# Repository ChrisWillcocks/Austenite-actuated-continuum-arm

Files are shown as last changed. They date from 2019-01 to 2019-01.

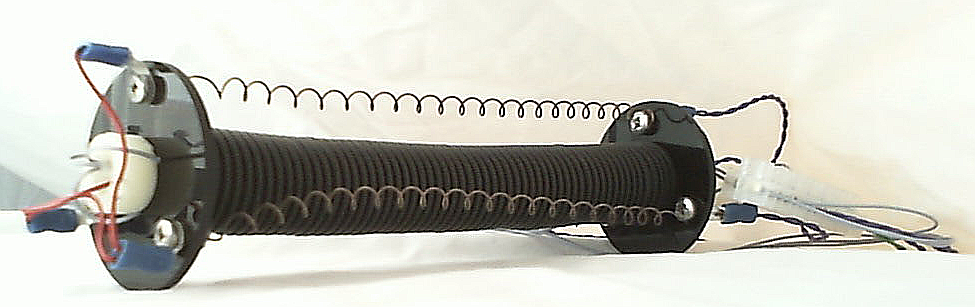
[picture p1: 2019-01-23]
hardware/snake-segment.png

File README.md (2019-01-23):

# Austenite-actuated-continuum-arm

Thesis for my MSc. Project used nitinol shape memory alloys as novel actuator for a modular snake arm robot. Thesis presents background, methods, testing and results.
Nitinol actuators are completely silent, extremely compact, and cost is comparable to existing electrical motors.

Modular chassis designed in FreeCAD. Basic testing software programmed on Arduino in C, electronic diagrams included.

Key conclusions are
- Best SMA actuators are bundles of thin (150um) wires. 
- SMAs can be modelled as a spring whose spring constant is a function of austenite to martensite ratio. Suitable for compliant actuators.
- Austenite ratio is a function of input power.
- Austenite ratio can be measured via electrical resistance (though exceptionally noisy). 3rd order elliptical filter found to reduce noise effectively.
- Heat hysteresis, the biggest drawback of SMAs, can be partially overcome with antagonistic pairs and optimal heating algorithms.
- Coil-type actuators provide largest stroke, but tend to keep heat inside the coil, exacerbating hysteresis. Improved cooling strategies could mitigate this.

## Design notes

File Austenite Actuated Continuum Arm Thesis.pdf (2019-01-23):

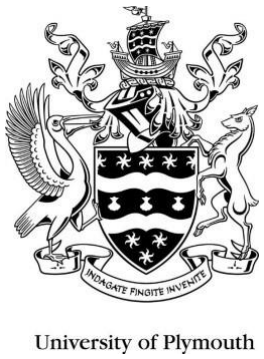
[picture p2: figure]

# Austenite Actuated Continuum Arm

# Chris Willcocks

### Supervisor: Dr D. Jenkins

## A thesis submitted to Plymouth University in partial fulfilment of the requirements for the degree of: Master of Science, Robotics

September 2018

School of Computing, Electronics, and Mathematics Faculty of Science and Engineering

Acknowledgements

I would like to extend my gratitude to Dr David Jenkins for his timely advice and invaluable

guidance across this project as supervisor.

I would also like to extend my thanks to the technicians of Smeaton Labs, for their technical

guidance.

### Declaration

________________________________________________________________

I confirm that I have read and understood the Plymouth University regulations relating to Assessment Offenses and that I am aware of the possible penalties for any breach of these regulations. I confirm that this is my own independent work.

Candidate’s Signature:

Chris Willcocks | Date: 2nd September 2018

Supervisor’s Signature:

Date:

Second Supervisor’s Signature:

Date:

### Copyright & Legal Notice

This copy of the dissertation has been supplied on the condition that anyone who consults it is understood to recognize that its copyright rests with its author and that no part of this dissertation and information derived from it may be published without the author’s prior written consent.

The names of actual companies and products mentioned throughout this dissertation are

trademarks or registered trademarks of their respective owners.

Abstract

Electric motors have been the de-facto standard actuator for robotics for close to half a century.

They offer high efficiency, torque, speed and extensively developed controllability. However,

miniaturisation is challenging, and dynamic factors such as collision response bandwidth are

limited, which pose major issues for safe human-robot interaction and operation in confined space.

In this work the viability of nitinol as an actuator in a continuum arm is investigated.

The main issues in using nitinol as an actuator are slow response due to hysteresis, very low

efficiency, low strain recovery and control of actuation.

The goal of the project is to produce an initial prototype as a functional test-bed for nitinol

actuation and future experimentation, as well as investigate the mechanical and electrical properties

of a nitinol actuator. To maximise strain recovery a coil type actuator was chosen, which has the

drawback of an inconsistent coil pitch during the cooling cycle. Methods to mitigate this are

proposed.

Experiments to characterise the mechanical and electrical properties of the nitinol sample were

performed.

Actuation is a function of martensite to austenite crystal ratio, which can be detected by

electrical resistance. Experiments were conducted to determine the resistance response across

actuation cycle, and in general were found to have a negative coefficient. However, significant

noise is encountered, which complicates using resistance as a sensing signal.

Finally, a number of recommendations are made for future study.

Contents

Abstract
4

Introduction
8

Outline
9

Chapter
1
– Literature review | 10
Discovery of the shape memory effect | 10
Basic principles | 10
Phase changes | 10
Structure | 11

Pseudo

-elasticity | 12
Current uses | 12
Major limitations | 13

Chapter
2
– Controller development | 15
Introduction | 15
Method | 15
Temperature sensing | 16

Micro

-controller | 16
Driving current | 17
Measuring resistance | 17
Testing | 1
| 8
Driver | 18
Temperature | 18
Resistance | 18
Results | 20
Driver | 20
Resistance | 22
Discussion | 23
Conclusion | 24

Chapter
3
– Characterisation experiments | 25
Introduction | 25
Method | 25
Introduction | 25
Stress / strain | 25
Resistance response | 26

Filtering | 26
Results | 27
Resistance response | 27
Stress / strain | 28
Filtering | 30
Interval average | 30
Exponential filter | 31
Running average | 31
Discussion | 31
Resistance to temperature | 31
Stress / strain | 32
Filtering | 33
Conclusions | 34

Chapter
4
– Single segment | 36
Introduction | 36
Construction | 36
Spine | 36
Sensor design | 37
Testing | 38
Results | 38
Discussion | 40

Conclusio
n | 42

Chapter
5
– Project results | 43
Controller design | 43
Electrical resistance | 43
Continuum segment | 44

Chapter
6
– Project discussion | 45
Modelling | 45
Limitations | 45
Recommendations | 46

Chapter
7
– Project conclusions | 47
References | 49
Appendices | 51

List of Figures

Figure 1 – Actuator comparison | 13
Flowchart 1 – Main Loop | 18
Flowchart 2 – Read Temperature function | 18
Flowchart 3 – Read Resistance function | 19
Flowchart 4 – Read Position function | 19
Flowchart 5 – Set Position function | 19
Figure 2 – Temperature rise response | 21
Figure 3 – Temperature hold 40 Celsius experiment 1 | 22
Figure 4 – Temperature hold 40 Celsius experiment 2 | 22
Figure 5 – Temperature hold 40 Celsius experiment 3 | 23
Figure 6 – Temperature hold 50 Celsius experiment 1 | 23
Figure 7 – Temperature hold 50 Celsius experiment 2 | 24
Figure 8 – Temperature hold 50 Celsius experiment 3 | 24
Figure 9 – Temperature hold 60 Celsius experiment 1 | 25
Figure 10 – Temperature hold 60 Celsius experiment 2 | 25

Figure 11 – Temperature hold 60 Celsius experiment 3

26

Table 1 – Hysteresis overshoot | 26
Figure 12 – Resistance response to temperature sweep | 32
Figure 13 – Stiffness against temperature | 33
Figure 14 – FFT Frequency response | 34
Figure 15 – Low pass filtering | 35
Figure 16 – Interval average filter | 36
Figure 17 – Exponential average filter | 36
Figure 18 – Running average filter | 37
Figure 19 – Spine segment assembly | 43
Figure 20 – Spine segment prototype | 44
Figure 21 – Bend sensor assembly | 45
Figure 22 – Bend sensor motion response 1 | 47
Figure 23 – Bend sensor motion response 2 | 47
Figure 24 – Bend sensor motion response 3 | 48
Figure 25 – Displacement at 30 Celsius | 59

Figure 26 – Displacement at 35 Celsius | 59
Figure 27 – Displacement at 40 Celsius | 59
Figure 28 – Displacement at 45 Celsius | 59
Figure 29 – Displacement at 50 Celsius | 59
Figure 30 – Displacement at 55 Celsius | 59
Figure 31 – Displacement at 60 Celsius | 59
Appendix A – Controller circuit diagram | 60
Appendix B – Driver circuit diagram | 60
Appendix C – Thermistor circuit diagram | 60

Introduction

In 1958, dismayed at mountains of obsolete tooling, inventor George Devol was inspired to

develop a reusable machine. His eventual creation, the Programmable Article Transfer the

“Unimate” was used to move parts on car assembly lines, and revolutionised industry. At the time,

electric motors could not provide an adequate solution for the Unimate owing to insufficient power

density, and so the Unimate was a hydraulic machine, which “leaked like a sieve”. Despite these

issues, the Unimate was a huge success, and remained the de-facto industrial robot until the

development of the Stanford arm. The Stanford arm was a purely electric robot, and was portable

enough to take to interview, where its abilities to move precisely into position using inverse

kinematics gave a significant advantage over existing hydraulic machines.

Over more than half a century, robots have cemented themselves in industrial applications,

where their repeatability, precision, and endurance have proved invaluable. However, robots have

largely stayed in these positions.

Two major limiting factors are size and power output (O’Toole, 2011). Standard electric motors

have undergone significant miniaturisation, even to the point of single molecule motors, but this

results in reduced power output.

Partial solutions to this problem have been found, such as the Laser Snake by OC Robotics (OC

Robotics, 2012). This robot uses tendons to mechanically link a bank of remote motors to a

segmented body. This retains much of the accuracy of a standard robotic arm, while removing the

weight of electric motors from the robot body and greatly reducing the robot’s size. However, the

size is still limited by the diameter and number of tendons. Most standard motor technologies suffer

from this limitation of physical dimensions.

Other motor technologies exist alongside electric motors, hydraulics and pneumatics, such as

piezoelectric elements, ultrasonic motors and polymers, but these typically do not have the stroke or

force output to be suitable for existing robotic applications. One promising alternative actuator is

the Shape Memory Alloy (SMA). Many SMAs exist, but of particular interest, due to ease of use

and power density, is nitinol.

In terms of size and power, the shape memory alloy nitinol offers a promising alternative. As reported by Teh (2008) “shape memory alloys show one of the highest work densities at 10e7 Jm⁻³ ,

which is a factor of 25 times greater than the work density of electric motors”.

Nitinol offers a number of benefits over other actuators, primarily in terms of a very compact

form factor. Other benefits include the potential for very low power, noiseless operation (O’Toole,

2011), compliance and ease of assembly.

Despite these potential advantages nitinol suffers from a number of drawbacks which prevent more

widespread adoption, including very low efficiency, difficulty in control and significant hysteresis.

The aims of this project are to construct a prototype continuum arm and electronic controller as a

test bed for development of nitinol as a robotic actuator.

Outline

The following chapters provide background and context for the motivation and approach of this

dissertation. Chapter 2 details the construction of a high power driver with integrated resistance

sensing circuit. Chapter 3 details a number of characterisation experiments, most crucially the

resistance response across the martensite and austenite phases, and stress and strain curves. The

relationship between temperature and nitinol’s spring constant is found. Chapter 4 details how a

single segment of a continuum arm was developed, including flexible sensor feedback devices.

Experimentation to verify operation of the feedback sensors was performed. Chapter 5 details the

project results and chapter 6 presents a discussion on the findings. Finally, chapter 7 presents the

conclusions, with recommendations for future study.

Chapter 1 - Literature review

This chapter presents background and context for the project. A brief history of nitinol is first

given. The basic principles are covered, including the crystalline structure of nitinol, the low

temperature martensite and high temperature austenite phase, phase transforms including twinned

and de-twinned martensite, mechanical properties and electrical properties.

A brief introduction to existing applications is presented, including both research and

commercial efforts.

Finally, a review of major limitations to more widespread nitinol actuator usage are analysed

and discussed.

Discovery of the shape memory effect

The earliest documented discovery of the shape memory effect was recorded by Arne Olander,

a Swedish physicist. In 1932 he observed the shape memory effect (SME) in gold-cadmium.

However, shape memory alloys were not practical until the discovery of SME in nickel-titanium,

discovered partially by accident in 1961. William Buehler and Frederick Wang, working in the

Naval Ordinance Laboratory, had produced a new alloy material for rocket nose cones. During a

demonstration, a member of the audience held a small sample to his smoking pipe, and was quite

surprised when it began moving.

Nitinol began to see major applications in the 1980s, primarily in the medical sector as a result

of good bio-compatibility. Devices such as stents made use of the shape memory effect, which

could automatically expand from body temperature soon after insertion (Teh, 2008). More recent

uses include part of a tail control system in Festo’s BionicOpter dragonfly (Festo, 2011).

Although other alloys, such as Fe-Mn-Si, Cu-Zn-Ni and Cu-Al-Ni exist, “due to their

instability, impracticability (e.g. brittleness) and poor thermo-mechanic performance, NiTi-based

SMAs are much more preferable for most applications” (Jani et al., 2014).

Basic principles

Phase changes

The defining characteristic of a shape memory alloy is the shape memory effect. Put simply, a

shape memory alloy can change shape when subject to energetic events, such as thermal heating,

magnetic induction, radiation or electrical Joule heating (Kumar, 2014). This is achieved through an

ability to exist in two distinct crystal structures, the low temperature martensite phase, and the high

temperature austenite phase.

The martensite phase is characterised by a low Young’s modulus, easy deformation, low yield

strength (Jani), and higher electrical resistance (Ma, 2004) (Teh, 2008).

The austenite phase is almost the inverse of the martensite phase; a much higher Young’s

modulus, highly recoverable strain, much higher yield strength, and lower electrical resistance. The

changing electrical resistance is of particular interest, as it is a measure of the austenite to

martensite ratio, rather than the electrically induced heating (Ma, 2004).

The potential for use as an actuator exists in this phase change. During deformation in the

martensite phase, a stress will produce a strain, and the strain will remain when the stress is

removed. During the austenite heating phase, this strain can be recovered, resulting in high

actuation potential (Jani et al.).

Structure

Twinned martensite: During the austenite phase the SMA’s crystal structure changes to be cubic

(Gorbet. R, 1996), and this structure remains when cooled, resulting in twinned martensite. The

cubic, twinned martensite will undergo a process known as de-twinning when subject to an external

load, changing the cubic martensite into rhombohedral de-twinned martensite. Essentially, the SMA

must always be “pulled” into a rhombohedral structure.

At low temperatures, the SMA will consist of 100% martensite. In the case of Joule heating,

which this project investigates, the SMA must be raised to the austenite start temperature, at which

point martensite will begin changing into austenite.

At the austenite finish temperature, the SMA is 100% austenite. The SMA then needs to cool

down to the martensite start temperature for martensite to begin forming, and the SMA will be fully

martensitic at the martensite finish temperature.

Typically, the martensite and austenite start and finish temperatures do not overlap, producing a “wide thermal hysteresis loop” (Teh, 2011, pg 10).

During the martensite phase, the SMA will display characteristics of a very soft spring, and is

capable of recovering a small amount of strain. If the applied stress exceeds the martensite yield

strength, the SMA will deform plastically. Further applied stress beyond this point will again cause

the SMA to behave elastically, until a yield point, beyond which strain becomes unrecoverable (Teh,

pg 35).

One-way shape memory effect:

Most commonly, SMAs make use of the one-way shape memory effect. An external stress

induces strain, and deforms the SMA into the martensite phase. Upon application of energy, austenite forms, and the shape memory effect occurs, returning the SMA to some remembered

shape. In the case of the coil SMAs used in this project, this has the effect of reducing the coil pitch

and length (Jani et al).

Two-way shape memory effect:

Much like the one-way effect, the two-way effect will recover a shape after deformation when

energy is applied. However, upon cooling, the SMA will also recover a remembered shape. When

compared to the one-way SME, the two-way effect requires training cycles (heating to one

remembered shape, and cooling to a second), deteriorates more quickly, and produces less strain

(Jani et al.). For these reasons it is commercially less attractive.

Pseudo-elasticity

Recovered strain is observed without application of energy. Typically, this is achieved by

having the austenite start temperature somewhere below room temperature, and finds common

application in fishing lines and braces, where the robustness of nickel-titanium is highly attractive.

Other transformations exist, such as rhombohedral and bainitic transformations (Jani et al.)

(Teh), but these are beyond the scope of this dissertation.

Current uses

Nitinol currently finds a number of commercial uses. Pseudo-elastic nitinol is used a fishing

leader (maybe description?), where the highly recoverable strain prevents kinking and provides a

more robust alternative to steel leaders (edge-techind.com, 2015).

Nitinol finds extensive use in the medical industry, where its physical properties and excellent

bio-compatibility are highly beneficial. Stents can be set to have an austenite finish temperature

matching internal body temperature, providing easy martensite insertion, and automatic expansion

when at the target site. However, these applications are essentially single-use, passive applications

of nitinol. Other applications making active use of nitinol include the Festo BioniCopter, which uses

nitinol elements to control the tail for lightweight, in-flight manoeuvrability. Use in aeroframes in

the pseudo-elastic phase has been achieved for vibration damping (Zhang et. al, 1996).

Compared to other technologies, nitinol is capable of producing significantly more stress than

even hydraulic actuators as a function of weight, though the potential of scale is uncertain, a

significant work volume, and a power volume greater than other actuators with the exception of

piezoceramics (Jani et al., pg1082).

O’Toole has investigated the use of nitinol in prosthetic limbs as a small-profile actuator, due to

nitinol’s low weight, high energy density, ease of integration, and silent operation.

His findings and conclusions are that force output from nitinol increases as per area, but so does

required current. Therefore, nitinol size selection should be determined by transient response to

applied current. Thinner wires appear to be a generally better approach, as thicker wires have

“severely diminished performance during natural cooling activity with significant relaxation times

evident”. Improved performance was seen in larger bundles of smaller wires, and a time delay “of

0.1-0.3 seconds” has been reported.

Interestingly “maximum strain is independent of wire diameter”, which implies a very small

necking region before unrecoverable damage is incurred. More predictably, as straight wire nitinol

was used, recoverable strain was relatively low, as O’Toole reports “strain observed in bundles is

approximately 3.6%”.

Holschuh et al (2014). have investigated the use of SMAs in active compression garments.

Their approach was to use coil actuators, which was found to produce “large recoverable

displacements (>100% in length)”.

Their findings are that “low spring index NiTi coil actuators … can produce large

displacements and… forces in a form factor that closely resembles a typical textile fibre”.

Major limitations

A nitinol actuator offers unparalleled advantages in terms of size and power to weight ratio, but

currently suffers from several severe drawbacks. The most pressing of these issues are low

recoverable strain, low accuracy, very low efficiency, controllability, and low actuation frequency

(Jani et al.)

Low strain

Figure 1 - actuator comparison

Strain within a straight nitinol wire is quite low. Plastic deformation will occur at 8% (Teh), and

most applications will keep strain well below this limit, often at 4% or less, as reported by O’Toole

with straight wire actuators. Holschuh et. al have demonstrated a solution to this issue through the

use of coil-type actuators, however Jani notes that this geometry of nitinol suffers from inconsistent

uncoiling.

Low accuracy

Teh reports that considerable improvement in nitinol control has been achieved, primarily

through PWM, PID and feed-forward control, however, the main limitations come from

“nonlinearities such as backlash-like hysteresis and saturation effects”, which are inherent to nitinol

and difficult to account for in any control system. This is also reported by Lange, G et. al(2015),

who conclude using an adaptive PID controller can compensate for the non-linear behaviour of the

material.

Low efficiency

As a heat activated SMA is a essentially just a heat engine, the maximum efficiency is

determined by the temperature delta. As an example, if a nitinol sample achieves austenite finish at

353k, and martensite finish at room temperature of 298k, the absolute maximum efficiency would

be 15.58%. This is before considering other inefficiencies, such as losses to atmosphere,

inefficiencies in power supply, and control limitations.

As reported by Jani et al. “Theoretically the maximum energy efficiency of SMAs is in the

range of 10–15%, which may fall to 10% based on the Carnot cycle efficiency in some studies, and

is often less than 1% in practical applications”.

Slow response

One of the most significant drawbacks with an SMA actuator is the very slow response, the low

actuation frequency and narrow bandwidth. The issue again lies primarily with nitinol being a heat

engine. Several studies (Qiu, 2001, Featherstone, 2006, Chee, 2005) have found that applying large

currents can overcome the slow heating phase. Another approach is to use nitinol with small volume

to surface area, as reported O’Toole and supported by Jani. However, the cooling phase is still

problematic, owing to the need for the heat to disperse through the body of the SMA via the surface

area. According to Jani et al. “the most significant concern in band-width limitation is the very slow cooling process, where the heat energy removal rate is limited by the mechanisms of heat

conduction and convection.”

Many studies have investigated resolving this issue, including using conventional heat sinks,

Peltier devices, convective cooling (air and liquid), and passive cooling. Although each approach

does improve performance, the trade-off is often in additional mechanical complexity, noise, energy

requirements, size and weight, all factors which SMA actuators are generally selected for.

Long-term life

Care must be taken when straining SMAs, and all SMAs suffer from life-cycle limits. Straight-

wire SMAs can recover 4% strain, and when pre-loaded, can recover up to 7% by pre-straining.

However, previous studies have found that overstraining nitinol results in reduced stroke over

operational lifespan. As reported by Jani et al. “SMAs have been shown to exhibit a softening of

behaviour (i.e. reducing the amount of recoverable strain) as the actuator is cycled, … by heating

and cooling the SMA under load”.

For this reason, keeping stroke and strain within operational limits is of vital importance.

Chapter 2 – Controller development

Introduction

In this chapter the development of a nitinol controller is detailed. A high power driver is

implemented using an N-channel MOSFET, and a programmable micro-controller used to modulate

applied power. A temporary thermistor is used to detect temperature changes for experimentation

and avoid overheating the nitinol. A resistance sensing circuit is developed to test the viability of

using resistance as a feedback mechanism for current control.

Method

A primary goal of this research is to develop a controller suitable for use with a nitinol actuator.

Currently, no commercial-off-the-shelf solutions exist for driving nitinol. As such, a major

focus of this project will be in the design and implementation of suitable driver circuitry. To achieve

this, two sub-circuit elements will be developed: the first will be a driver capable of delivering high

current to the nitinol element, the second will be a sensing circuit which will determine resistance

across the nitinol. During development, measuring temperature directly will also be necessary, as

resistive values for martensite and austenite phases are not typically available.

Once the hardware is constructed, a suitable control method will be implemented. The initial

control methodology will be a bang-bang driver. This simple approach has been chosen for rapid

development, but will also allow for measurement of nitinol’s heat cycle response to input power,

and allow for measurement of the resulting time lag. This simple control methodology would be

unsuitable for more advanced use, such as positioning.

The nitinol must not be overheated. Initially, the temperature will be monitored with a

thermistor, as this will produce more accurate and more reliable results than measuring resistance,

and does not require calibration or tuning. This has the obvious limitation of being unable to check

temperature across the entire length of the nitinol coil. To overcome this during initial

characterisation experiments, the thermistor will be inserted through the centre of the coil, and the

coil hung vertically. This will aim to minimise temperature read errors.

Ultimately, a better approach to preventing overheating is required. As reported by Ma,

resistance varies with the changing ratio of austenite to martensite. Measuring resistance therefore

gives indication of phase state, and is robust against external factors like ambient temperature,

although the relationship is highly non-linear.

Temperature sensing

One issue of concern with nitinol is overheating. As reported by Jani and Teh, if the nitinol is

allowed to overheat, degradation of the shape memory effect can occur with extended usage. To

prevent this, careful monitoring of the temperature must be achieved.

At the project outset, measurement of resistance was selected as an approach to measure

temperature. This was to then be used to control the nitinol phase state, after determining the

austenite and martensite start and stop temperatures. However, according to Ma, the resistance is

actually a function of the proportion of martensite to austenite. This actually proves beneficial, as

the need for extrapolation is removed, and phase change can be measured directly. In theory, by

measuring when the resistance change stops, the austenite finish temperature can be determined,

and the heating phase can be optimised. This relationship can then be used to control applied power,

applying only as much power as necessary to bring the nitinol to the austenite finish temperature.

This will be more fully explored in chapter 3.

Feedback on the temperature of the nitinol still remains vital, in order to prevent overheating.

Initially, a thermistor will be used, which proved to be an appropriate approach while the nitinol

was kept in the coiled state, and the entire element was be in close proximity to the thermistor.

However, as the nitinol will be stretched when mounted on the continuum arm the thermistor will be unable to effectively read the temperature across the entire nitinol sample. As such, the relation

between temperature and resistance will be investigated in chapter 3.

Micro-controller

A suitable micro-controller needs to be selected for centralised control of the driver. The micro-

controller must be able to transmit data to a computer for further processing, have access to a

number of analogue inputs, and be capable of producing PWM drive signals. Sufficient code space

so as to allow for flexible development will also be beneficial. For these reasons, the Atmega328

was chosen as the primary development platform.

Driving current

Nitinol, in both phases, has very low resistance. The martensite phase was measured at 1.5ohms

on delivery. Teh reports the use of high currents, both to overcome the slow heating cycle, and to

provide large actuation forces. Therefore, the most appropriate driver would be a power MOSFET,

capable of handling high current, with a very low Rds-on value. As the MOSFET will be passing

large current values, a MOSFET which can easily be driven to saturation from the ATmega328 will

be necessary.

The nitinol sample’s resistance is very low, measuring 1.5 ohms when fully martensitic at room

temperature. Nitinol typically requires high current to operate as well, meaning that any switch must

have a very low on resistance. For these reasons, the IPP072N10N MOSFET was selected, owing to

an Rdson of 7mOhms and a gate threshold voltage of 3.5V, allowing for easy saturation driving. N-

channel MOSFETS are easier to source, therefore the driver circuit was designed as a low-side

switch.

Owing to the low electrical resistance of nitinol, the driver circuitry will not need to provide a

high voltage. For initial testing, a 1A supply will be used, which would thus only require 1.5 volts

to conduct. This will later be increased to 3A, which is the highest current that can be driven from a

5V supply. The earliest prototype test driver, driven by the supply voltage, drew only 3.6V, only just

turning the MOSFET on. This was remedied once the micro-controller was used to drive the

MOSFET.

Measuring resistance

The analogue pins of the Atmega328 are only capable of measuring voltage. Therefore, to

measure the resistance through the nitinol, each nitinol element was built into a voltage divider. To maximise sensitivity, the sensing resistor was chosen to be a close match to the measured resistance

value of 1.5 ohms. Due to this low resistance the sensing resistor resistor will experience a high

current and there exists a potential risk of overheating. Therefore, the sensing resistor’s power

rating will need to be a minimum of 5W, and the closest commercial solution was 7W. For

simplicity of construction, the driving voltage will also be used as the testing voltage. The testing

sub-circuit must be activated periodically, to prevent the sensing resistor from overheating.

Although this approach reduces accuracy, construction is greatly simplified.

The micro-controller’s built-in ADC has a resolution of 10 bits, allowing for a sensitivity of

0.0049V. This can be improved by using the internal 3.3V supply as a reference voltage, increasing

sensitivity to 0.0029V. The current PSU is capable of supplying 1A, which for the 1.5ohm nitinol

will require a maximum of 1.5V, well within the saturation range the 3.3V reference voltage causes.

The circuit diagram can be found in appendix A.

Algorithm

The algorithm for the experimental driver follows the flowchart listed below. As temperature

sensing via the thermistor is unsuitable during standard operation this is considered a non-

mandatory process.

The nitinol resistance is also unsuitable for use as a positional feedback sensor, as resistance is

dependent on crystal formation, which is independent of machine position. Therefore, a position

sensing subroutine is implemented. The development of the sensor type is described in chapter 4.

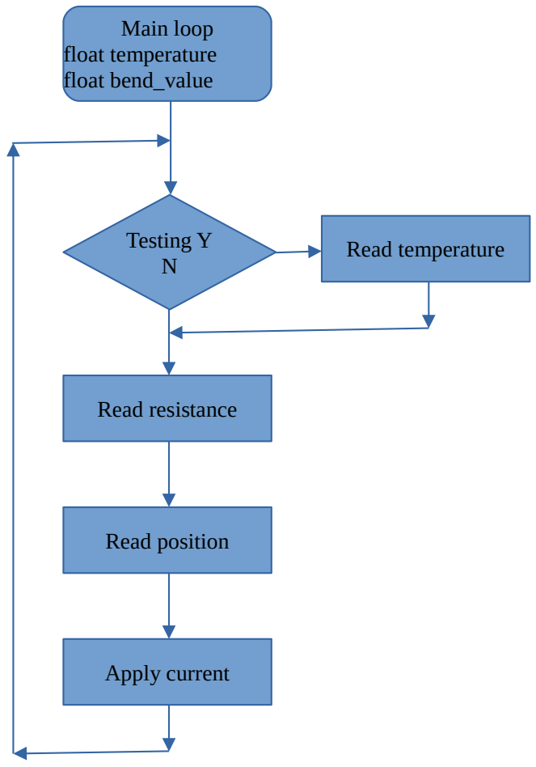
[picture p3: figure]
Main loop float temperature float bend_value; Testing Y N; Read temperature; Read resistance; Read position; Apply current
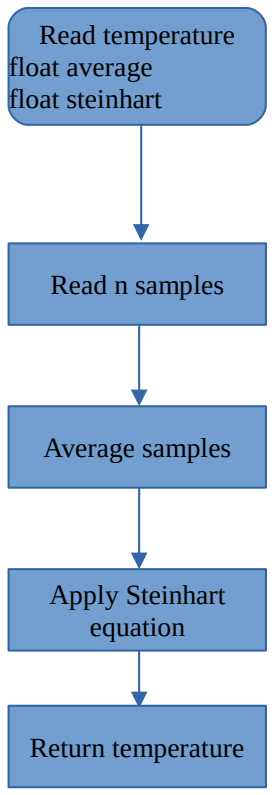
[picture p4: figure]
Read temperature float average float steinhart; Read n samples; Average samples; Apply Steinhart equation; Return temperature
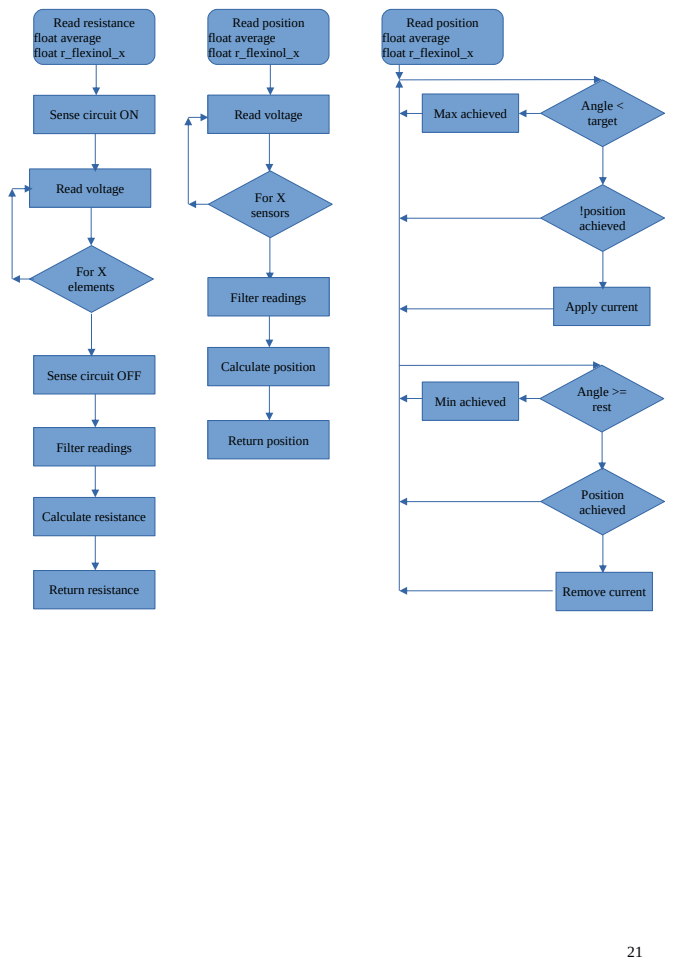
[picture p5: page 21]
Read position float average float r_flexinol_x; For X sensors; Read voltage; Filter readings; Calculate position; Return position; Read resistance float average float r_flexinol_x; For X elements; Calculate resistance; Return resistance; Max achieved; Angle <; target; !position achieved; Apply current; Position achieved; Angle >= rest; Remove current; Min achieved

Sense circuit ON

Sense circuit OFF

Testing

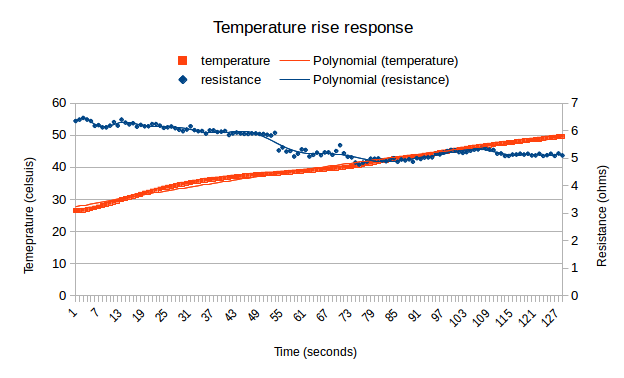
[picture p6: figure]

Driver

After circuit assembly and continuity checks driver operation was assessed by connecting a

sample of nitinol and checking for current flow and temperature increase using the thermistor.

Temperature

The heating capacity of the driver circuit, the accuracy of the resistance sensing circuit, and the

heat capacity of the nitinol were tested. A simple bang-bang controller was used, first to bring the

nitinol to a target temperature, and then to hold at the specified temperature. An additional benefit

of this simple control scheme is the ability to observe temperature lag through the nitinol sample.

The expected heat response would be an oscillation around the target temperature. The resistance

was expected to change during the heating phase, and remain unchanged during the cooling phase,

as no external load will be applied.

A nitinol sample was received in the zero-pitch configuration and connected to the test driver.

The thermistor was inserted through the centre of the nitinol to obtain an even sampling of heat. A

simple bang-bang controller was written to bring the nitinol sample to a selection of temperature

increments, hold at the target temperature, and record resistance.

Figure 2- temperature rise response

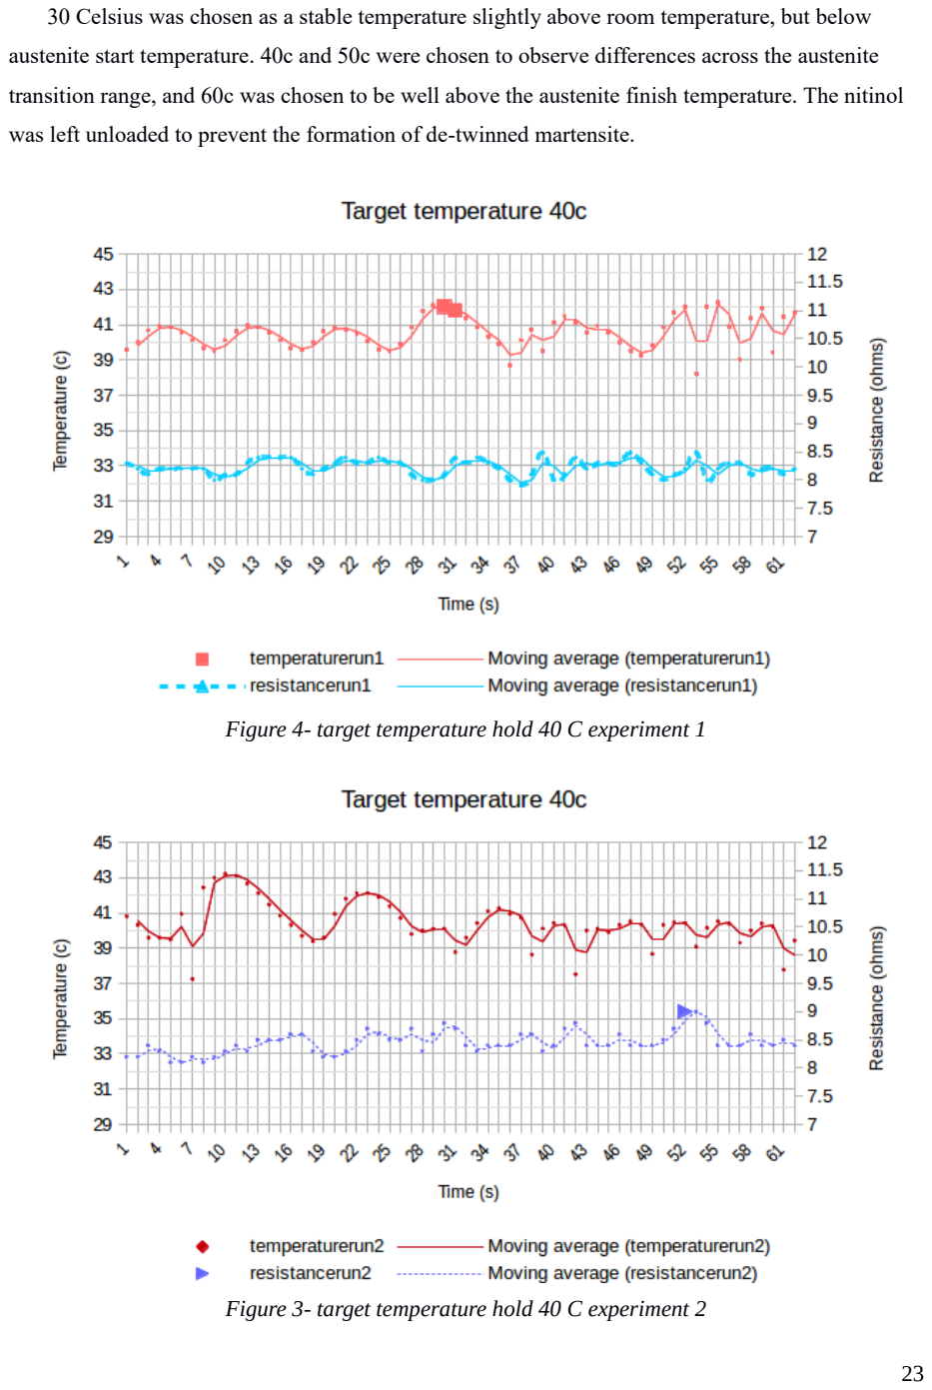
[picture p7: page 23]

30 Celsius was chosen as a stable temperature slightly above room temperature, but below

austenite start temperature. 40c and 50c were chosen to observe differences across the austenite

transition range, and 60c was chosen to be well above the austenite finish temperature. The nitinol

was left unloaded to prevent the formation of de-twinned martensite.

Figure 4- target temperature hold 40 C experiment 1

Figure 3- target temperature hold 40 C experiment 2

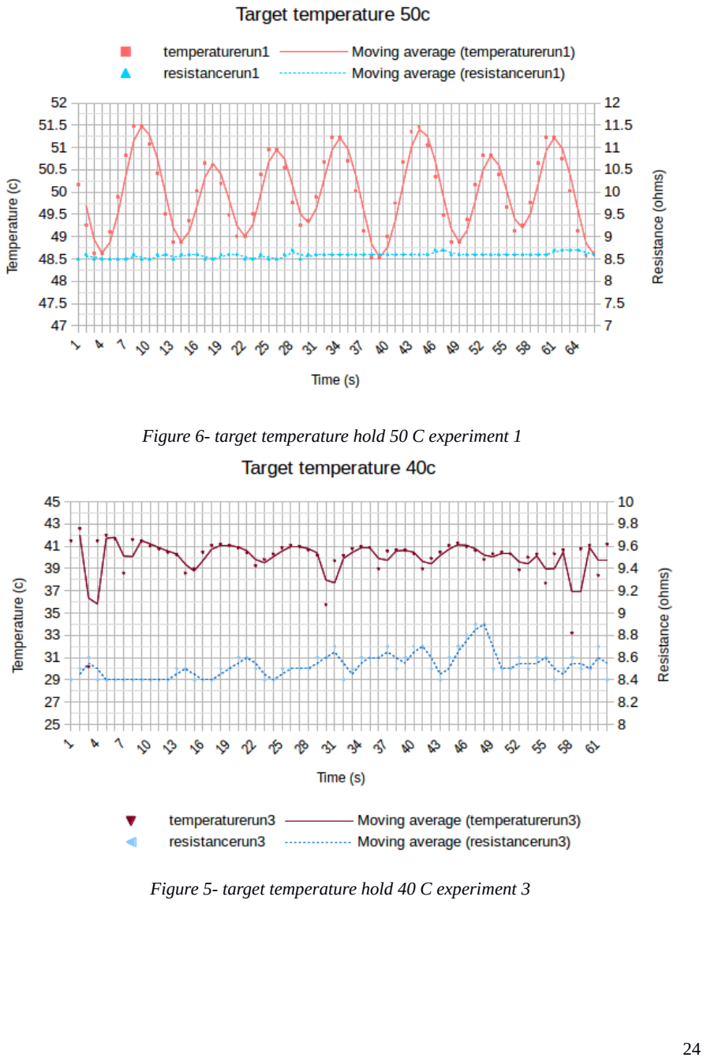
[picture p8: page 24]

Figure 5- target temperature hold 40 C experiment 3

Figure 6- target temperature hold 50 C experiment 1

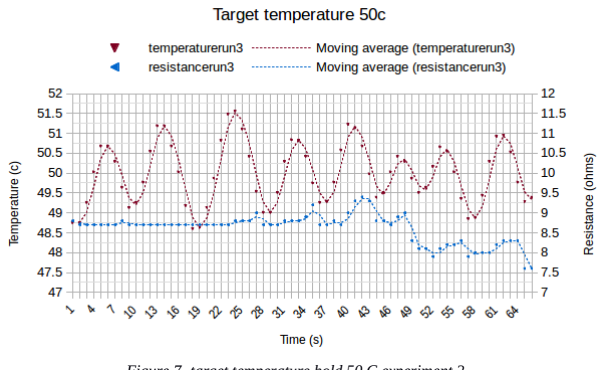
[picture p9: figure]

A simple program was written to poll the analogue input connected to the thermistor. The thermistor

was left to record room temperature, and the results sent via a USB link to a desktop PC.

Figure 7- target temperature hold 50 C experiment 2

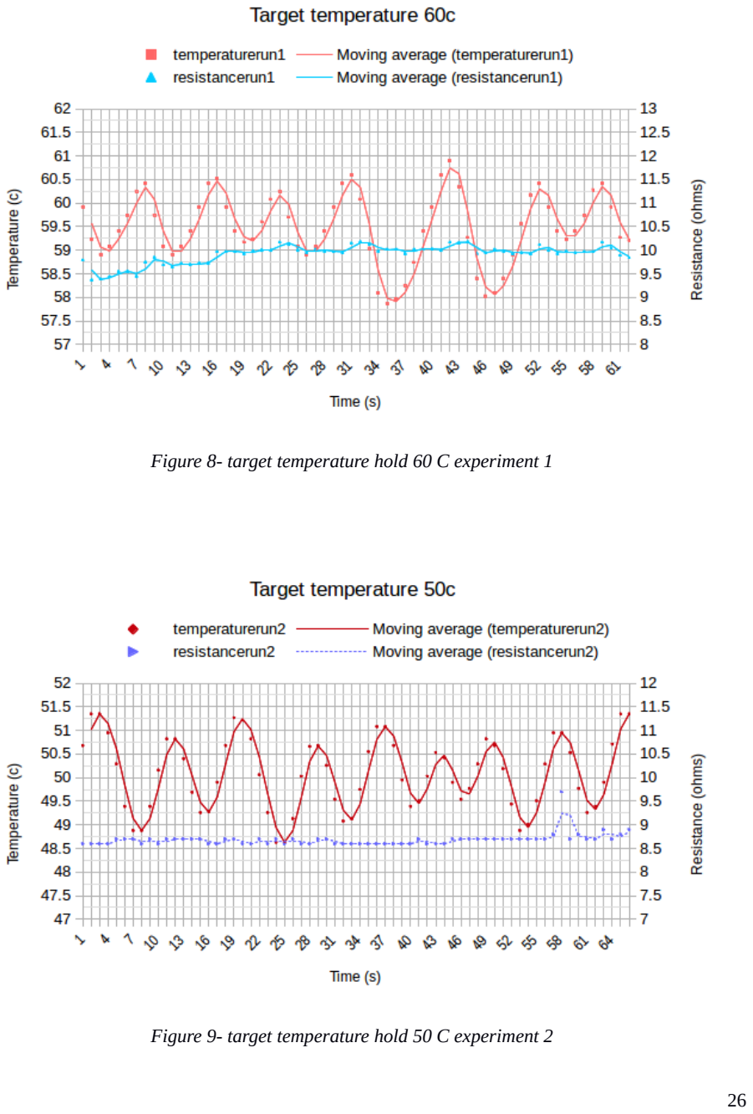
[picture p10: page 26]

Figure 9- target temperature hold 50 C experiment 2

Figure 8- target temperature hold 60 C experiment 1

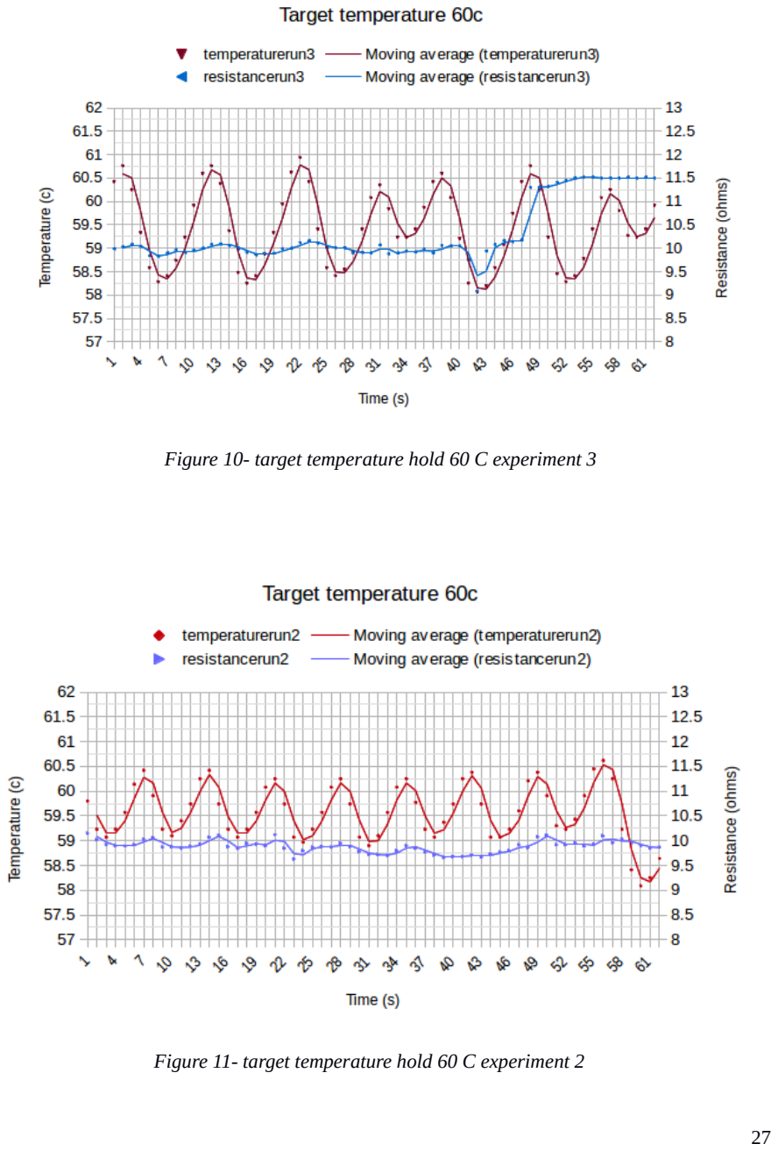
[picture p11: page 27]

Figure 10- target temperature hold 60 C experiment 3

Figure 11- target temperature hold 60 C experiment 2

Resistance

The existing program was expanded to poll the analogue input with the sensing circuitry. The

power side of the driver was left in the on state, with the sensing side pulsed periodically to measure

the nitinol’s resistance. The measured resistance was sent via the USB link to a desktop PC for

recording in a csv file and further analysis. To minimise the sense circuit’s effect on the nitinol’s

temperature sampling was kept at low frequency (1Hz).

Results

Driver

The MOSFET is capable of supplying the nitinol current without any issue. No complications

were experienced in circuit usage. The thermistor and controller arrangement are able to report the

temperature of the nitinol without complication.

Using the N-channel MOSFET as a low-side switch keeps the circuit cool throughout

operation, implying good efficiency. Predictably, using the N-channel MOSFET as a high-side

switch results in overheating, which would need to be resolved with a P-channel MOSFET and an

additional driver transistor interfacing the micro-controller.

A very slow rise time is observed, where the nitinol takes over 2 minutes to achieve 50 Celsius.

During this time a resistance step drop can be observed. The temperature change also experiences

non-linearity, with a period of slower change midway through the rise.

The sample was heated to increments of 40C, 50C and 60C, maintained at target temperature

for 1 minute, and electrical resistance recorded. Each experiment was repeated three times.

Holding the nitinol at each temperature increment resulted in expected hysteresis. This

temperature hysteresis can be mostly explained as a result of the bang-bang controller, and would

be resolved with incorporation of a complete PID feedback loop.

A number of dips were recorded during the 40 Celsius holding experiment. More significant

changes in nitinol resistance also occurred after the temperature was maintained for an extended

period, most notably in the third experiment.

Table 1 shows the temperature overshoot and undershoot of each target temperature. In general,

overshoot is worse at lower temperatures, and undershoot worse at higher temperatures, which can

be attributed to the power supply. The 1 Amp supply was able to bring the nitinol sample to a

maximum temperature of 73c during testing, and the nitinol could be brought to higher

temperatures with a more powerful supply. This again demonstrates the hysteresis effect inherent to

nitinol.

Overshoot (s) | 40 Celsius | 50 Celsius | 60 Celsius
Minimum | 0.70 | 2.30 | 1.00
Average | 3.00 | 3.20 | 1.40
Maximum | 6.70 | 4.00 | 2.00

Undershoot (s)

Minimum | 0.00 | 2.30 | 3.30
Average | 0.60 | 2.80 | 4.60
Maximum | 2.00 | 3.70 | 5.70

Table 1 – Overshoot due to hysteresis

Resistance

The circuit displays the capability of measuring the small resistance through the nitinol sample,

implying a 10-bit resolution is sufficient. At rest, the measurement appears noisy, implying noise

during measurement is an issue to consider.

Between the temperature rise and temperature hold experiments there is a notable change in

resistance, despite similar temperature ranges. This can be attributed to the nitinol being moved

between experiments, and martensite forming, causing the higher resistance seen in the temperature

holding experiments. This is an issue to consider for future experiments.

The resolution of the on-board ADC was found to be sufficient for measuring the nitinol’s

resistance. The power driver was kept in the on state, to test for future controller operation. This

provided two conductive paths for the sensing signal, and as such the true resistance value is not

reported to the controller. However, resolution and repeatability were not affected, and due to the

improved simplicity of hardware and software design, this approach was kept, as loss of true

resistance is not detrimental to operation.

Further analysis on noise and response times in is explored in the following chapter.

Discussion

The first major improvement this design would require is improved noise prevention. At

present, the sensing circuitry uses the same supply voltage as the driving sub-circuit, which

introduces additional noise components.

Initially, the sensing resistor was in series with the nitinol element. This caused excessive

heating of the sensing resistor, even when specified for operation with high power, and inhibited

performance of the nitinol element. This would strongly suggest an integrated driver/sensing circuit

is impractical.

A more suitable design would require proper circuit isolation. With the low-side N-channel

MOSFET, this is presently impossible, and would require a high-current P-channel MOSFET in

what would essentially be an OR’ed power supply configuration.

Isolating the sensing voltage would also have the benefit of allowing for greater power to be

applied to the nitinol. At present, the Atmega328 can only accept 5V on the analogue input before

damage may occur to the board. At its nominal resistance of 1.5 ohms, the nitinol is limited to only

3.3A, well below the 25A used in other studies. This is sufficient for the current project, but would

encounter problems with greater quantities of nitinol, particularly bundles, and applications

requiring higher current drive for faster heating cycles.

Some potential may exist for use of the MOSFET’s Rdson as the sensing element, if full circuit

isolation were either undesired or impractical (such as space saving configurations) but this would

require a very linear Rdson or a complex model to account for the non-linearity.

A very slow rise was observed during the temperature rise experiment. This can be attributed to

the low current of the supply (1 Amp), and the changing crystalline structure. Initially, the nitinol

would have been pure martensite, but as the temperature increased lower resistance austenite

developed, allowing for increased current flow and increased joule heating. The reduction in

heating rate can be explained by saturation of the power supply’s heating capacity.

A step-drop in resistance close to 39c was also noted. This step change was also noted in further

experiments, discussed in chapter 3. The most likely cause is the change in crystalline structure,

which also implies that the transition occurs quickly. The literature, including Teh and Ma, report

that the nitinol phase transform occurs across a temperature range, however the presence of the step

change may imply a significant proportion of that change occurs across a much narrower range.

Noise in the resistance readings is noticeably larger at 40 Celsius. This is likely caused by the

nitinol being partway through the early stages of its phase change, and the crystalline structure is

changing in a non-linear manner.

As the driver sub-circuit is still enabled and drawing current the true resistance is not read.

However, this approach does not detract from performance, as each nitinol element would require

individual calibration in any case. The repeatability of the readings and clear delineation of

resistances demonstrate that relying on relative values should prove a valid approach.

The 10-bit resolution is sufficient for use with a 3.3V reference voltage. However, at higher

currents a greater voltage will be passed across the device, which will cause the ADC to saturate.

The ADC can be re-referenced to 5V, reducing sensitivity to 0.0049V, which may still prove

sufficient for low-power operations. However, at much higher power additional interfacing circuitry

would be required.

Conclusion

A simple yet effective driver circuit has been developed, which is capable of bringing a nitinol

sample to austenite finish temperature. A slow heating cycle is observed, which can be improved

though use of a power supply capable of delivering greater current. Scalability may be an issue, as

each controller would only be suitable for up to three elements, meaning the current driver design is

suitable only for a single continuum arm segment.

A resistance sensing circuit was designed and constructed. The circuit is generally capable of

measuring resistance as the nitinol sample’s crystalline structure changes. However, noise is a

significant problem.

Chapter 3 - Characterisation experiments

Introduction

This chapter details characterisation experiments performed to analyse nitinol’s response to

input power. Resistance across temperature ranges was first explored, and resistance is confirmed to

be dependent on strain. Resistance across varying strain is measured and analysed. Considerable

noise is encountered in resistance measurement, therefore filtering experimentation was performed.

Finally, actuation response to input power was investigated, by varying the temperature in the

nitinol, and recording displacement. Finally, the stress, strain and spring constant of nitinol was

found.

Method

Introduction

Electrical driving of nitinol actuators requires precise control over internal crystalline ratio.

Typically, this is measured through temperature, but a thermistor is unsuitable for a continuum arm

robot and coil-type nitinol. The most readily available method for crystal ratio detection is via

electrical resistance, therefore a number of experiments will be performed to determine the

relationship between temperature and resistance.

For actuation purposes, the stroke of the nitinol must be determined. As nitinol can be modelled

as a spring this is effectively determining the strain, which is also dependent on a spring constant,

which should exist in the nitinol. It is hypothesised that this spring constant would be dependent on

the crystalline ratio, or more accurately would be proportional to the percentage of austenite.

Finally, the experimentation from the previous chapter has shown there exists considerable

noise in measuring the nitinol’s resistance, therefore a number of filtering techniques will be

investigated.

Stress / strain

The nitinol sample was hung from a retort stand, and stress was applied via gravitational force

from 50g masses. The resulting strain was measured against a ruler to 1mm precision, by capturing

position on a Microsoft lifecam HD3000, and GUVCview version 2.0.2.

The nitinol sample was electrically heated in increments of 5 degrees Celsius, and held at 30c,

35c, 40c, 45c, 50c, 55c, and 60c. For initial experimentation, the simple bang-bang controller was

re-used. Using this control scheme, hysteresis would still be present, and affect the experimentation,

however Teh and others report the presence of hysteresis even with more advanced PID control schemes. By using a bang-bang controller, the response of nitinol crystal phase change to input

power can be more easily observed, therefore the simpler bang-bang controller was chosen.

For the first experiment the nitinol sample was left unloaded, such that no force would be

applied during the cooling phase. The nitinol was then brought to the target temperatures and

maintained for 30 seconds. The sample was then allowed to cool back to room temperature.

Displacement against mass was plotted, and the spring constant k was found.

Resistance response

As previously stated, resistance is a function of crystal ratio, rather than temperature. By

measuring the resistance relative to total potential change, the martensite and austenite finish points

can be determined, and used to control applied current. For the resistance to temperature

experiment, resistance was recorded via the driver circuit.

To observe the relationship between temperature and resistance, the nitinol was cycled through

the entire available temperature range, from 30c to 60c, and the change in resistance recorded via

the driver/sensor circuit. 30 Celsius was chosen as the lowest because room temperature was above

25c at the time of experimentation. As resistance is a function of crystal ratio, and de-twinned

martensite only forms under strain, the nitinol sample was suspended from a retort stand, with a

100g mass attached to produce strain under gravity.

The raw resistance readings were recorded without any filtering applied, and were copied into a

spreadsheet for analysis.

Filtering

For the filtering experimentation, three filters were investigated; averaging, exponential

filtering, and rolling average. The unfiltered resistance values from the temperature/resistance

experiment were used to test each filter.

Averaging waits for the input of 10 measurements, then calculates the mean. The filter then

waits for an additional 10 measurements, and calculates a new mean.

Exponential filtering takes into account the entire history of the readings. Readings are

calculated from the equation of the form yn = w × xn + (1 – w) × yn – 1, where yn is the averaged value,

w is a weighting factor, xn is the new input, and yn-1 is the previous output. Each previous output is

then fed back into the equation along with a new reading, to continually produce a new average.

The weighting value can be tuned manually to optimise performance.

Finally, the rolling averaging takes a sample of 10 values, and calculates the mean. The samples

are then shifted, such that the earliest reading is discarded, and a new reading is added. This then

repeats for the duration of operation. Within the spreadsheet, this is accomplished by shifting the

sampled cell range. Within a micro-controller, this would be achieved by writing to an array, and

incrementing the array index, resetting the index when filled.

Results

Resistance response

During the cooling phase of the unloaded experiment, no change in nitinol resistance was

observed. This matches Ma’s observations and conclusion that resistance is a function of crystal

ratio rather than temperature.

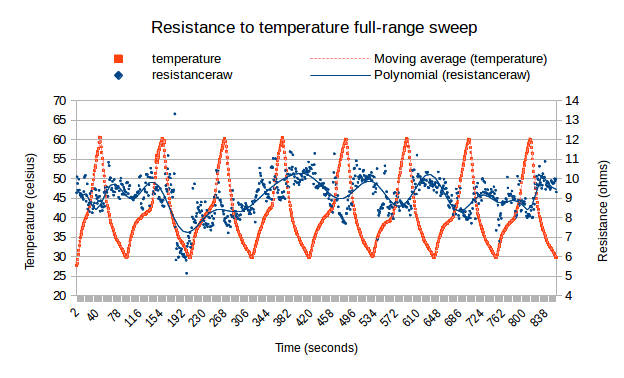
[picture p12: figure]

The second experiment, with an external load causing strain when cooled, produced a changing

resistance.

Figure 12 - resistance to temperature

Considerable noise is observed during temperature cycling, including a number of transient

spikes. The largest spike observed at 192 seconds is due to the operator’s erroneous mechanical

interference. While this affected the experiment, the data provides a clear relation between

resistance and strain, and demonstrates a sensitivity to mechanical interference. Of note are the start

and finish resistances, which fall within similar values and imply a degree of repeatability. The

changes in resistance value also remain within a similar range, further demonstrating a repeatability.

In general, the resistance changes show a negative coefficient, mostly present from 362 seconds

onwards. This effect is less pronounced at the start of the experiment, and required considerable

settling time after the mechanical disturbance.

Stress / strain

The results of the stress and strain characterisation experiments can be seen in the appendices,

in figures 14 through 20.

During the cooling phase the martensite was observed to have a long settling time where

displacement continued to progress. When loaded, nitinol would periodically extend, then stabilise.

The most likely cause for this behaviour is the bang-bang controller; each time the target

temperature was exceeded, the controller ceased applying current, and the load was able to cause

the nitinol to extend. For the experiment, this was resolved by recording via the camera before the

next off-cycle. Of note, this effect implies a control method to aid in mitigating the slow cooling

response of nitinol, and is expanded on in the discussion section.

This oscillation was most pronounced at 40 Celsius, with a mass of 150g, implying this

temperature is close to the austenite start temperature.

At higher target temperatures, the nitinol was able to recover a greater strain, demonstrating a

link between input power, crystal ratio and recoverable strain.

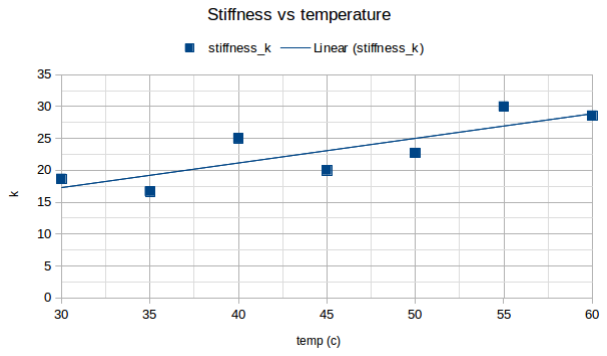
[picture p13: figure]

As can be clearly seen across each temperature increment, strain recovery increases

proportionally with temperature. This demonstrates an increase in the elastic limit of nitinol,

proportional to temperature, and an increased area where nitinol obeys Hooke’s law.

This is more clearly demonstrated in figure 21, where the spring constant was calculated across

each temperature increment. In general, stiffness increases with temperature, and therefore should

increase proportionally with austenite formation.

Strain recovery becomes linear after 50 Celsius, however it should be noted a maximum mass

of 200g was applied, and to fully measure nitinol stiffness against temperature force would need to

be applied beyond nitinol’s austenite yield strength.

The stiffness should in theory increase to some maximum value, which was not tested in this

project. Also of note is the recoverable strain. The nitinol was able to recover from 150mm of

deformation to 40mm at 60 Celsius, a strain recovery of 60%, significantly improved over the 4%

typically reported for straight wire nitinol.

Filtering

Figure 13- Stiffness vs temperature

Filtering was applied on the same resistance values recorded in the previous experiment. Three

filters were investigated; interval averaging, rolling average, and exponential filtering. The signal is

highly noisy, in part due to a lack of hardware level filtering. Resistance is hypothesised to be

primarily dependent on crystal ratio, which is in turn dependent on strain. As a result, nitinol is

sensitive to physical movement.

Frequency analysis

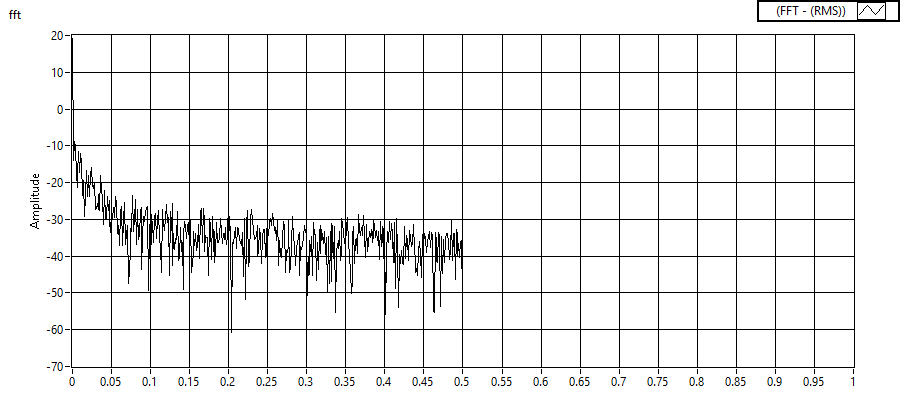
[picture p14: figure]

A frequency analysis was performed in Labview to identify the frequencies of concern with regards

to noise.

As the nitinol was powered from a DC source, only a 0Hz signal is desired. Noise appears

across all higher frequencies.

Figure 14 - FFT frequency response

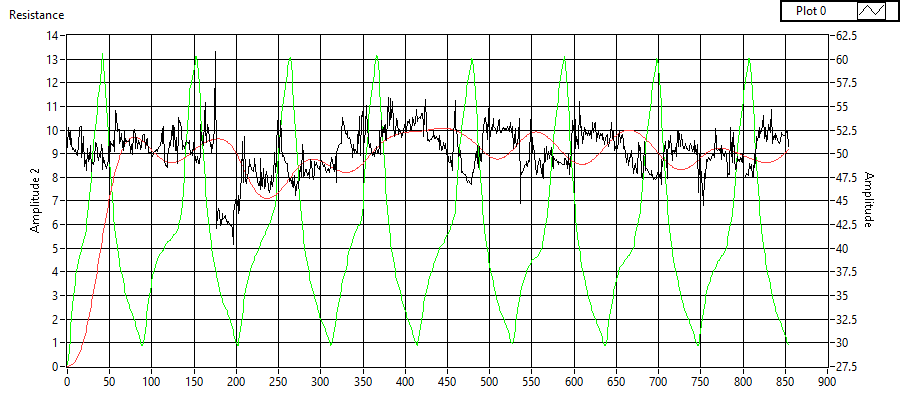
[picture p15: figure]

The effects of a low frequency filter were investigated, by applying a low-pass filter with a cut-off frequency of 0.01Hz. A 3rd order elliptical filter produced reasonable results. The green line

indicates the nitinol temperature, the black line the unfiltered resistance and noise signal, and the

red line the filtered resistance signal.
The 3rd order elliptical filter successfully removes the noise component, though introduces

considerable phase shift. The negative coefficient of resistance can be seen, although the subsequent

phase shift due to filtering has caused unacceptable signal lag. Of note is the recovery after

mechanical interference. The resistance of the nitinol appears to require several heat cycles to

renormalise, possibly due to incomplete formation of martensite after the undesired strain.

Interval Average

Due to the slow response of interval averaging a strong immunity to spiking is demonstrated,

though complete immunity is not achieved.

After the mechanical disturbance and settling period, a clear distinction between resistances can

be observed, though large spikes continue to introduce distortion. There is also notable signal loss,

owing to the very slow response time of interval averaging.

Figure 15 - Low pass filtering

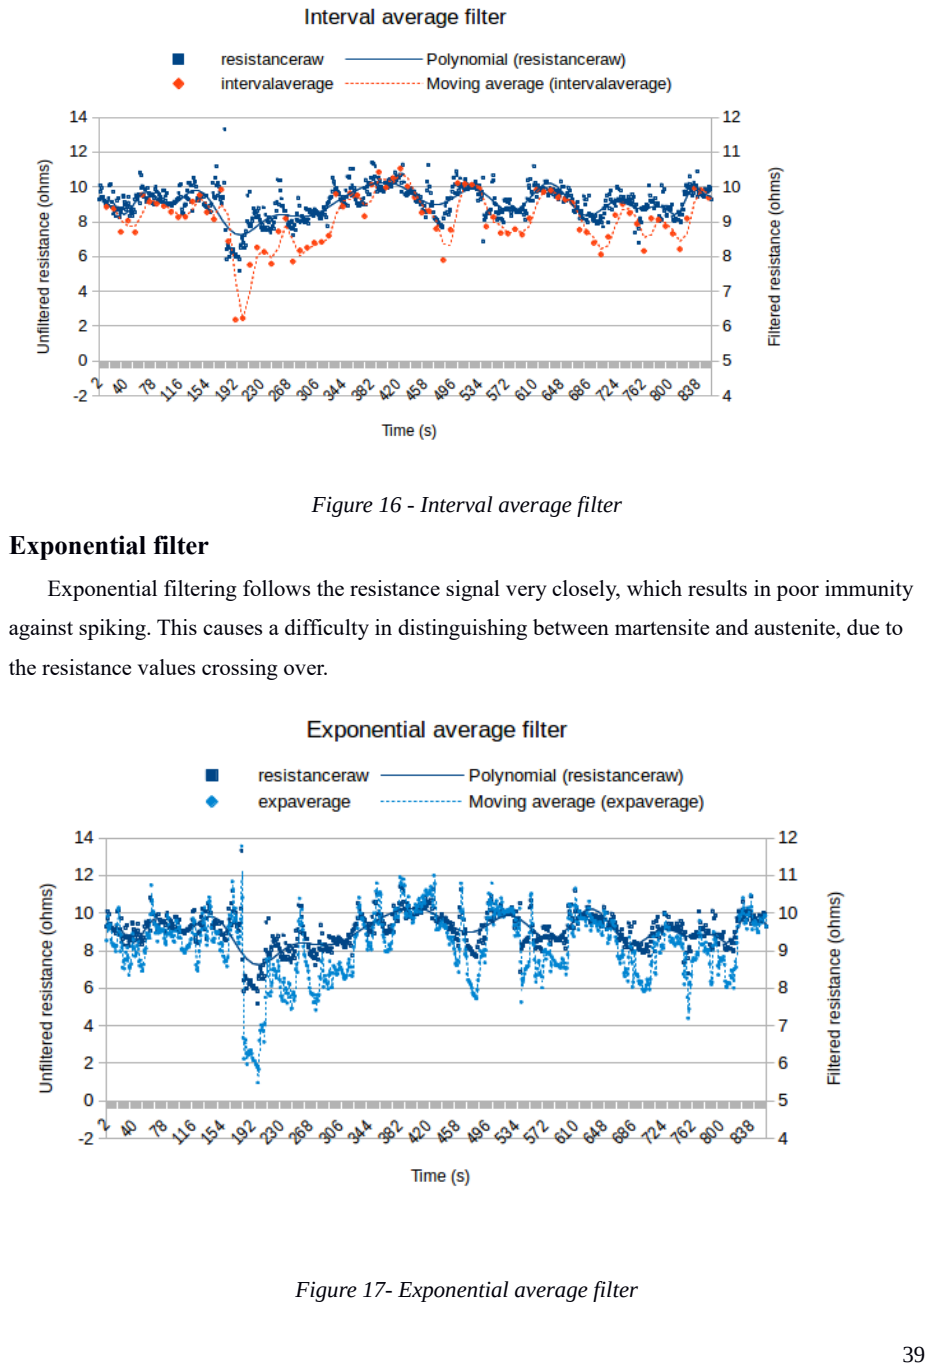
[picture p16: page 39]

Figure 16 - Interval average filter Exponential filter

Exponential filtering follows the resistance signal very closely, which results in poor immunity

against spiking. This causes a difficulty in distinguishing between martensite and austenite, due to

the resistance values crossing over.

Figure 17- Exponential average filter

Running average

The running average produce a more noticeable lag than the other two filtering methods, but

demonstrates good immunity against spiking. Similarly to interval averaging, a clear distinction

between high and low resistance can be observed, implying differentiation between martensite and

austenite is possible. Compared to interval averaging, running average follows the input signal more

closely, which results in spikes having a more pronounced effect, overcomes the signal loss issues

with interval averaging.

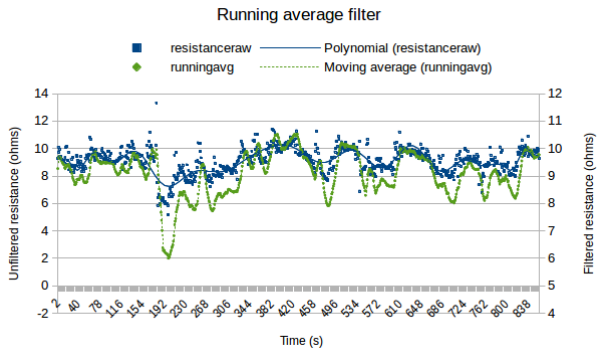
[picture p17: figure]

Figure 18- Running average filter

Discussion

Resistance to temperature

As resistance is a function of crystal ratio the resistance was hypothesised to be that of twinned

martensite immediately after an unloaded heating cycle. The austenite phase produces a cubic

crystal structure, which remains when cooled into twinned martensite. An externally applied load

will then cause the cubic twinned martensite to deform into rhombic de-twinned martensite. As both

austenite and twinned martensite share the same crystal structure, it was hypothesised that they have

the same value of resistivity. This is supported through observation of changing resistance with

applied strain.

Resistance measurement offers a possible method of detecting crystalline ratio. The crystal

ratio would essentially act as a method to prevent overheating the nitinol, by reducing current in

proportion with austenite formation. However, the significant noise encountered during

measurements makes precise calculation impossible. A significantly improved filter design must be

used to effectively use resistance as a proxy for crystal ratio measurement. This filter would also

need to account for mechanical interference, as as nitinol appears very sensitive to physical

disturbance,

The resistance of austenite and twinned martensite appear identical, and as a result, any system

measuring resistance would be unable to differentiate between these two crystalline forms. For

differentiation to occur, nitinol must be placed under stress to de-twin martensite, meaning a nitinol

actuator must be either biased with a return spring or part of antagonist pair. A systems could also

potentially use the two-way shape memory effect, but this approach was not tested in this project.

Another approach for measuring resistance is to measure current draw from a constant current

supply, which may produce a more stable result.

A different approach for future investigation would be to measure resonant response. As each

crystal structure is physically different, they should resonate at different frequencies, which may

provide a more reliable way of sensing crystal ratio, though dependence on external mechanical

interference though will likely remain an issue.

Stress / strain

From the experiments, nitinol demonstrates a variable stiffness that is proportional to austenite

formation. As austenite is proportional to temperature, which itself is a function of input power, this

would suggest a control system could be modelled to modulate input power to output force,

essentially producing an electrically variable spring as an actuator.

During the cooling cycle the nitinol experienced continued displacement, and this displacement

was not recovered during the heating phase. Potential causes for this behaviour are an insufficient

current supply or additional electrical resistance. The 1 Amp supply used during the experiments

produced a slow heating cycle, supporting this hypothesis.

A second potential cause for the impeded heating cycle is the formation of de-twinned

martensite due to strain, which has a greater electrical resistance and would reduce current flow. In

line with this hypothesis, the heating was observed to be much slower after significant strain.

This extension was most pronounced at 40 Celsius with a 150g load, where the nitinol was

observed to be oscillating. While this oscillation provided additional challenges during recording,

this effect offers a potential solution to the typically slow response of nitinol based actuators. The power into the nitinol can be controlled to achieve a desired stiffness, which is a product of

austenite proportion. By closely matching the spring stiffness to external force, which would be

determined by a bias force, antagonistic pair, and an external load, the response of a nitinol actuator

could potentially be greatly improved.

As reported by Holschuh nitinol can be modelled as a spring. The spring constant of nitinol was

calculated from the acquired stress and strain data, and can be seen to increase with temperature. In

general, nitinol’s stiffness increases with austenite, until at 100% austenite some maximum stiffness

is achieved.

One major issue, particularly with coil geometry nitinol, is an inconsistent displacement.

Generally, the nitinol sample will not maintain a single, consistent coil pitch along its entire length.

During very early testing stages, a disposable cigarette lighter was used to rapidly observe and

confirm the shape memory effect. This informal experimentation caused some coils to contract,

while the remainder of the sample did not. During testing, a similar effect was noted with electrical

heating; coils with a lower pitch than the rest of the sample displayed a more rapid shape memory

effect than coils with a larger pitch. The current hypothesis is that this is caused by an unequal

formation of austenite crystal. This problem compounds, as austenitic areas of the nitinol contract

faster, while martensitic areas fail to recover strain until they have sufficiently heated. This effect

was also noted by Jani, and is a concern with using coil geometry nitinol.

During the cooling phase, each active coil is able to heat and insulate its neighbouring coils.

The uninsulated coils at the extreme end of the nitinol are expose to air. Thus, the ends of the nitinol

cool faster, resulting in inconsistent martensite formation. A design to overcome this limitation

would require some insulation to ensure consistent and evenly distributed temperature. This would

overcome the primary issue with coil-geometry nitinol, and allow for exploitation of the

significantly improved strain recovery possible. However, it should be noted this would hinder the

cooling cycle. Therefore, an ideal solution be to use a controllable insulating device.

During testing the strain recovery distance became more consistent at 50 Celsius and above.

From these results, it is possible to infer that the austenite start temperature is 40 Celsius and the

finish temperature is 50 Celsius. This effect points to the possibility of a robotic system being able

to self-calibrate. Such a system would need to observe the response of austenite formation against

applied power, with a return spring of a known spring constant. This would likely need to be

performed in tandem with a positional sensor.

Filtering

The resistance of nitinol has proven to be an exceptionally noisy signal. The first major

improvement that needs to be undertaken in this regard is a filtered sensing signal, and a constant

current source.

A major issue with using resistance to detect changing crystal ratio is that the crystal phase

transform process is poorly understood. Many additional factors, such as crystal size, orientation,

density, placement, lattice structure etc. are outside the scope of this project, yet are likely to affect

the resistance readings. Sensitivity to mechanical interference has also been demonstrated as serious

issue for consideration.

An improved electronic construction design, with a sufficiently isolated sensing signal, and a

better understanding of the phase transformation characteristics are essential before effective

resistance sensing can take place.

Of the three filtering techniques tested, exponential filtering has the poorest response.

Exponential filtering has a very fast response, which renders it unsuitable due to nitinol’s slow heat

change characteristics. The fast response of this filter allows the higher frequency noise spikes to

pass through, as well as the much lower frequency nitinol resistance change.

Interval averaging produces a much improved response, returning a value closely matching

nitinol’s resistance change. Due to the amplitude and low frequencies of the noise spikes

considerable noise continues to pass through and affects the final value. However, a clear

delineation between resistance values can be read.

The running average filter produces similar results to the interval averaging, though with some

offset delay introduced, and slightly greater sensitivity to noise. However, this approach has the

benefit of providing a real-time response, as opposed to the interval averaging response, which

produces only very periodic output. The running average would however produce the heaviest

computational load, as it would need to be implemented as an array. Using the ADC value of the

Atmega328 as an integer, a 10-element array would require 20 bytes, which can be handled within

the micro-controller, but may introduce difficulties in scaling, as the micro-controller would require

20 bytes per element.

The most effective approach to filtering nitinol actuators for effective resistance sensing is to

design an extremely low frequency filter, where the frequency is close to the expected rate of

change of the nitinol.

Conclusions

The nitinol was placed through a powered temperature cycle and the change in resistance was

recorded. A clear negative temperature co-efficient can be observed, and reasonable repeatability is

achieved, seen at the start and end of the temperature cycle. However, significant noise is

encountered, which makes reading the signal exceptionally difficult.

Recovered strain was measured against a range of temperature values. In general, a greater

strain recovery is observed with an increase in temperature. From these experiments, the spring

constant of nitinol was calculated, and has been demonstrated to increase with applied power.

A number of filtering techniques were evaluated. In general, a low frequency filter produces the

best results.

Noticeable oscillation was observed at a temperature of 40 Celsius, with an attached mass of

150g, implying an improved response time, and a potential method to reduce hysteresis by

controlling input power to match spring constant to external load.

Chapter 4 - Single segment

Introduction

The construction of a single continuum arm segment is presented. A low-cost approach with

readily available materials was taken, to provide the greatest flexibility and modability during

development. A feedback device was required; custom bend sensors were designed, constructed and

tested to determine viability for a continuum arm robot.

Construction

Spine

The single segment for the continuum arm needs to displace the end effector through a

consistent rotation and translation, to minimise kinematic modelling complications. A number of

mounting points are required to provide suitable options for mounting the nitinol actuators, and for

experimentation with sensors. Finally, this should be achieved with low-cost, readily available

components for easy construction.

The prototype should also be designed with scalability in mind, such that the design could be

adapted for a range of scenarios.

Two approaches for chassis design were identified: universal joints or a continuum arm.

Universal joints are able to constrain movement to two axes; this would be beneficial for the

addition of encoders for positional feedback, and provide easier precision control. However, this

introduces considerably increased design and manufacturing complexity, and the motion precision

will likely be lost with the use of nitinol as the actuator.

The second approach is to use a flexible continuum arm, making the robot partially a soft robot.

This approach provides the distinct advantage of easy manufacture and assembly from readily

available materials, and easy modability for sensor and actuator mounting. For these reasons, the

second approach was chosen.

The chassis of the robot is constructed of two distinct elements: a spine and two end cap discs.

The spine element needs to be flexible, but must also be incompressible, as any compression would

simply result in lost actuation potential and complexities in measuring deflection. To achieve this,

PVC tubing was selected, which had the benefit of easy interfacing through the use of tubing

connectors.

During bending, the PVC tube can buckle if bent too far. The PVC also requires some way of

returning to the straight position after actuation. To achieve this, a compression spring with a

closely matching diameter was used as a support and return mechanism. Finally, to isolate the spring from other conductive elements, and to provide additional environmental protection for the

segment, a shroud was applied. For this prototype, this took the form of cable conduit.

Any sensors and nitinol elements require mechanical mounting points, and the return/support

spring requires an element to hold the assembly together. This is done through a set of discs, acting

as end caps for each segment. The discs are pinched between the compression spring and the

shoulder of the tubing connectors. The discs are constructed from acrylic, and can be easily

machined to provide mounting points for any additional hardware. Figure 25 shows the assembly

for the prototype.

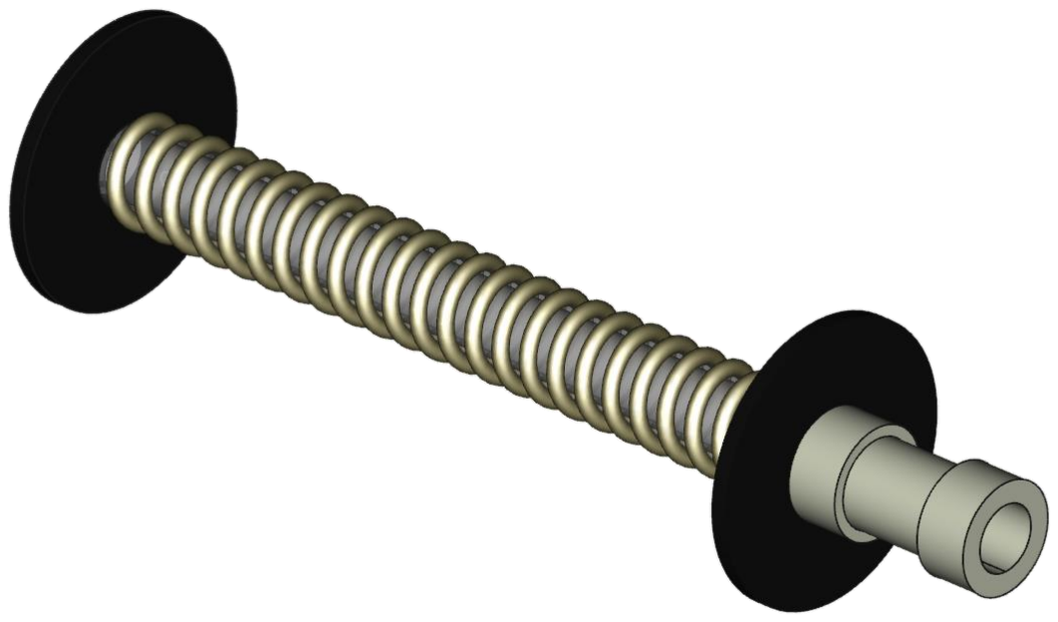
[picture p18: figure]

Figure 19 - Spine segment assembly

Following on from common industrial design practise (OC robotics, 2015) three nitinol

actuators were placed around the spine at 120 degrees. This provides a complete three-dimensional

control solution with the minimum number of actuators.

For ease of control, the sensors and actuators should align, with both components placed at 120

degrees around the spine. The discs were machined to include aligned mounting points. Each nitinol

actuator was mounted to the disc via a bolt through the mounting point, which then also acted as the

electrical connection. Finally, each disc has a small slot machined to allow for electrical connection

of each sensor, and to assist in alignment of actuator and sensor. The physical prototype is shown in

figure 26.

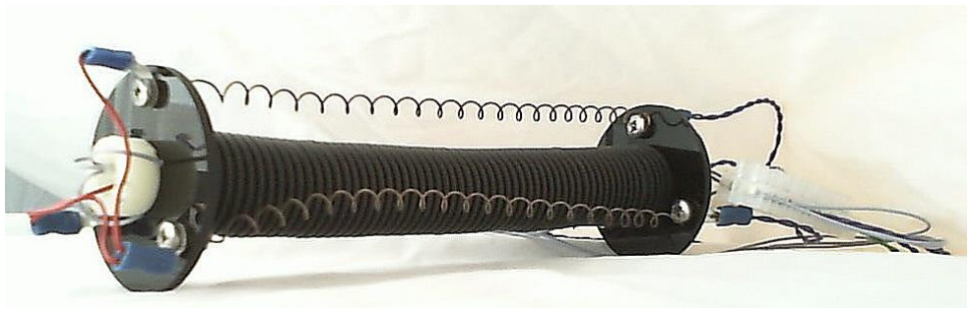
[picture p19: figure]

Figure 20 - Spine segment prototype

Nitinol resistance provides feedback on the current stage of its phase transform, but not on position

or strain. If the robot is to be used when unobservable, such as in a pipe network, using a control

scheme such as head-following, or fully autonomous, some form of positional feedback is needed.

Sensor design

For a flexible robot segment, rigid encoders do not provide an adequate solution. Most suitable

positional feedback devices would also be flexible, such as a strain gauge. Most commercial

solutions are the wrong size, too expensive, or both, so the decision was made to build custom

sensors. A resistive element will change resistance when deformed. Two conductive elements can

sandwich a resistive element, be encompassed in a flexible insulation element, and provide a robust,

reliable bend gauge.

The initial bend sensors had excessive resistance (greater than 1M ohm), and could not pass

sufficient voltage for sensing on the Atmega32, which recommends a maximum input resistance of

less than 10K ohms. A number of steps were taken to remedy this. The resistance was reduced to

acceptable levels by first reducing the length of the resistive element, increasing its width,

increasing the length the conductive element contacted the resistive element, and finally layering

multiple resistive elements in parallel. The entire sensor was constructed on a single adhesive

backing which adhered to the flexible spine, allowing for a minimal profile sensor. The assembly is

shown in figure 27.

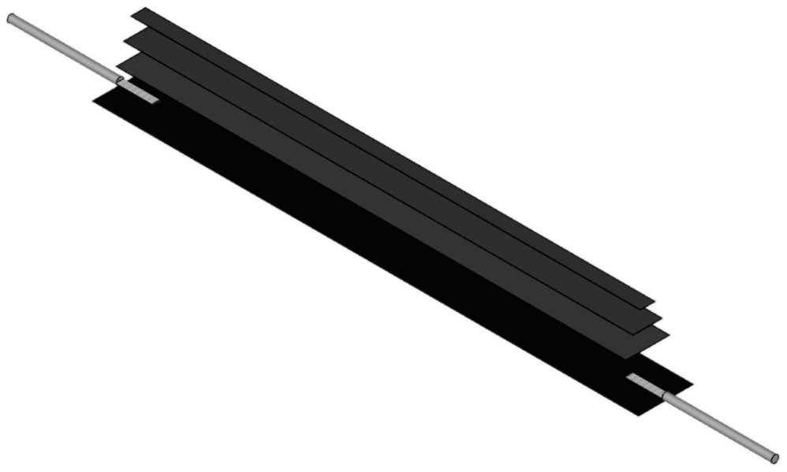
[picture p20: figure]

Figure 21 - Bend sensor assembly

Testing

A new circuit was constructed to measure and log the bend sensor resistance. The flat resistance

of each bend gauge was tested with a multimeter and a closely matching resistor was selected to

make a voltage divider. The voltage divider output was fed into the ADC of an Atmeg328, which

then transmitted the data over USB to a desktop computer.

The reference voltage was set to 3.3V, providing a resolution of 0.0029V which, for a sensing

current of 200mA, would allow for a maximum sensitivity of 0.0145 ohms, which should be

sufficient for this experiment.

All three bend gauges were constructed and mounted on the single segment body. The single

segment body was clamped vertically to mitigate bend due to gravity and recorded while stationary.

This established the resting resistance.

The single segment was bent in the direction of each individual sensor, and the change in

resistance recorded. Finally, the single segment was rotated by hand to observe the change in

resistance across all elements simultaneously.

Results

Across all three experiments a very stable response was generated, with a maximum deviation

of less than 1K ohm. There is notable variability within each sensor between each test, in each case

having the identical deviation of an increasing resistance. This can be explained as each sensor

having a much higher resistance than recommended for the Atmega328.

Owing to small inevitable variabilities during construction, each sensor has a unique resistance.

Since the same resistance value was chosen for each voltage divider the resting resistance differs

between sensors.

Bending each individual sensor, the relationship between resistance and angle can be observed

to change linearly. Little disturbance from noise is present, even without any filtering techniques.

One major issue encountered is the exponential decay back to the resting position. This can be

explained as a result of the resistance of each sensor being above the recommended limit for the

Atmega328’s analogue inputs. Because of this, the capacitance present in the Atmega’s internal

architecture is unable to charge back to supply voltage in a reasonable time frame.

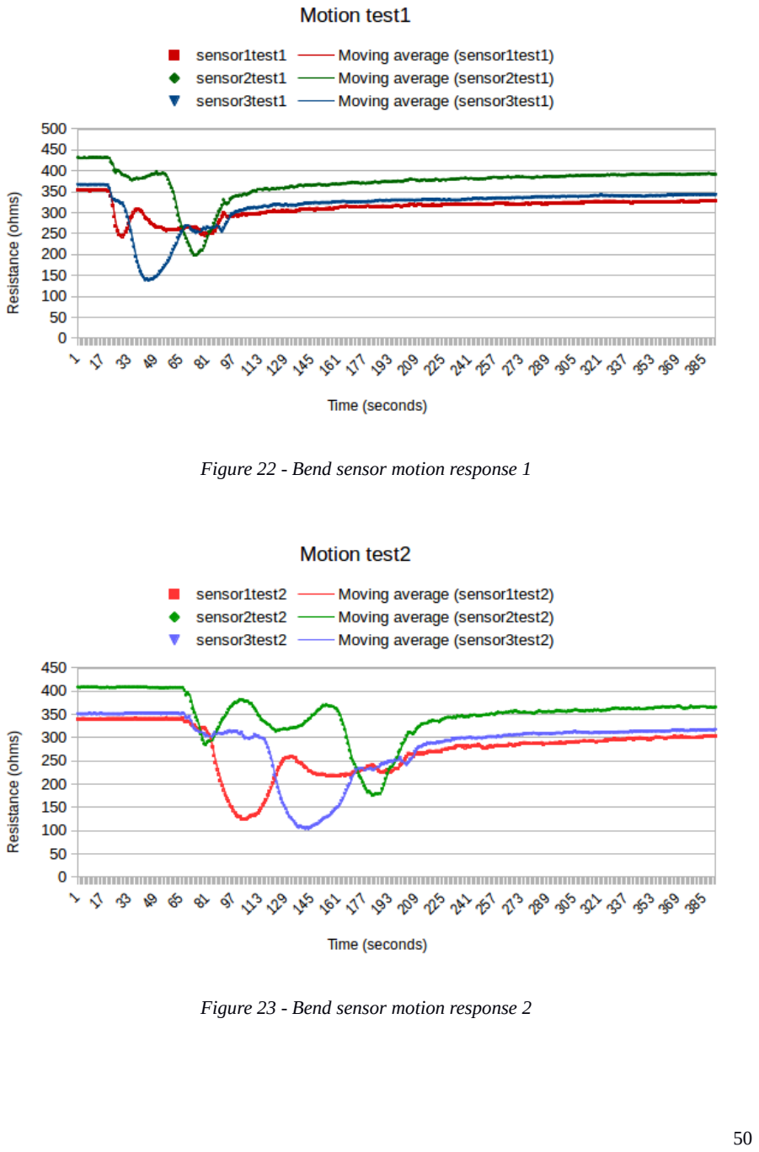
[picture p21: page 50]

Figure 22 - Bend sensor motion response 1

Figure 23 - Bend sensor motion response 2

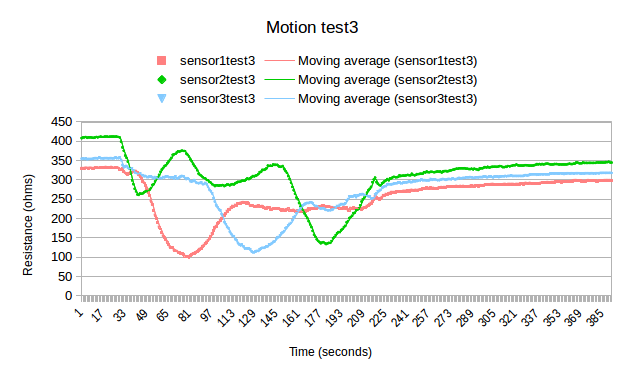
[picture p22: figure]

Figure 24 - Bend sensor motion response 3

Bending and then rotating the single segment, a clear phase offset is visible between each

sensor, showing a delay of 120 degrees, which corresponds well with the physical position of each

sensor. The amplitude then corresponds to the angle the sensor is bent to.

Each sensor also displays a secondary resistance change, which is caused by the bend sensor

detecting deformation in both longitudinal directions. As a resistance change is caused by a

clustering of conductive elements along one side of the bend sensor, the current sensors are unable

to differentiate between bend directions.

During assembly, the nitinol was strained to 180mm, and resistance was found to increase from

1.5 ohms to 25 ohms. The nitinol was returned to 1.5 ohms with a brief application of heat.

Discussion

Construction proved challenging, but produced a robust prototype. The most pressing issues

with current construction include the compression spring damaging the bend sensors, insufficient

bend sensor adhesion, insufficient lateral flexibility for the bend sensors, and the final assembly

holding together via tension.

The spine spring needs to be carefully selected to match stiffness with nitinol elements. The

other components used in spine construction contribute to overall stiffness and require state space

analysis for optimal construction and control.

PVC tubing, compression spring and hose connectors provide a robust, low cost solution, but

cause complexities in assembly, due to several elements exerting tension and friction. An approach

allowing for easier assembly might be to use goose-beck tubing and bayonet connectors.

The custom bend sensors lacked sufficient adhesive surface to properly remain attached to the

PVC tube. This is partially resolved with the use of the compression spring, and has so far survived

several hours of operation, but a more robust approach is needed. Dedicated bend sensors with

lower resistance, and greater lateral flexibility to accommodate the flexibility of the segment would

improve performance. Despite these issues, the sensors have good accuracy, resolution and

repeatability, offering benefits for such a low-cost approach.

The current design allows for excellent mechanical and electrical mounting of the nitinol

actuators, with the option of quickly and easily adding additional nitinol elements as required.

The observed bend sensor phase offset could be used for calibration. Each nitinol element

would be commanded to heat through a sine wave cycle with 120 degrees of offset and the bend

sensor response would be observed. The bend sensor response can then be used to calculate actual

physical position of each sensor.

Despite the limitations observed with the custom built sensors, bend sensors appear to be a very

suitable sensing element for a continuum arm approach. Even low-cost sensors display good noise

immunity and repeatability. The issue of capacitance due to excessive resistance could be solved

with suitable commercial sensors, a design modified further to reduce resistance, or interfacing

circuitry.

The presence of a changing resistance in both directions could cause errors in positioning, if the

robot does not know which way it is bending. This can be resolved by measuring the deformation of

all three sensors simultaneously.

The resistance change in each nitinol element was anticipated, though larger than expected. As

observed with the informal method of heating, the nitinol’s resistance can be conditioned to bring it

within specification. This would form part of a set of conditioning routines necessary after segment

production, which could be achieved with the existing driver circuitry.

Conclusions

A functional single segment continuum arm was produced, which acts as an acceptable test bed

for further study. Material choice requires refinement, particularly with regards to matching body

stiffness to nitinol actuation response, in order to optimise performance.

Bend sensors are a suitable approach to feedback in a continuum arm. Future bend sensors need

to have a resistance matched to micro-controller specifications, improved adhesion, and improved

lateral flex.

Chapter 5 - Project Results

In this chapter, the results of each preceding chapter are summarised and compared with the

established literature. The effectiveness of the chosen approaches are evaluated, and

recommendations are made for future study.

Controller design

High power MOSFETs are a suitable solution for nitinol driving. To overcome the slow

response during the heating cycle high current should be applied, though this would typically be for

a relatively short duration, as austenite ratio can be maintained with lower power. Throughout this

project, a very slow heating response time was observed, due to the low current capacity of the

available PSU.

The response time of the cooling cycle is still a major issue. The use of large gauge nitinol

contributes to this issue, as internal heat takes a longer time to diffuse through the material and

conduct to atmosphere. The findings from this project correspond with O’Toole’s findings that

thinner gauge nitinol is a more suitable approach for higher frequency response.

One of the key findings of this project is the potential to counteract the slow response of the

cooling cycle through use of an external load. By applying an external force with a load bias or

antagonist pair strain can be induced much more quickly in a cooling nitinol actuator, potentially

greatly improving response times. The precise mechanism by which this occurs is not fully

understood, as martensite should not begin forming until the martensite start temperature is

achieved. Therefore further work in this area is required.

Electrical resistance

Measuring resistance has proved to be difficult, owing to the presence of severe noise. This

noise is generally of much higher frequency than the nitinol response, and the severity of the

amplitude would prevent reliable measurement of crystalline ratio. An improved electronic design

should be used to help mitigate the noise issue.

The resistance is also highly sensitive to mechanical disturbance. This is due to the formation of

martensite, which has proved beneficial in improving actuation response times, but largely prevents

using resistance as a sensing method for determining crystalline ratio. Mechanical disturbance may

be causing unevenly distributed strain within the nitinol.

No change in resistance was heat cycled without strain, demonstrating that resistance is a

function of crystal ratio.

From the heat cycling experiments, nitinol’s resistance can be observed to have a negative

temperature coefficient. This also demonstrates that martensite crystal has a higher electrical

resistance. This higher resistance impedes current flow, and contributes to the slow heat cycle

response.

During the temperature and displacement experiments, strain recovery was found to increase

with temperature, as a result of greater austenite formation, and a greater shape memory effect

response. As nitinol can be modelled as a spring, displacement can be modelled as a function of

force to spring stiffness, which is proportional to input power.

Nitinol response is very slow due to hysteresis and the slow crystalline phase change, therefore

very a low pass filter is likely the best candidate for resistance signal conditioning and good

operation. The running average filter produced the best results in the experiments in this project.

Continuum segment

A continuum arm segment was easily constructed from low-cost, readily available materials,

demonstrating the viability of a continuum arm approach. Currently, a large part of the structure is

maintained by tension and friction, most notably the tubing connectors to the PVC tube spine, and

the compression spring and acrylic discs. This has proved acceptable for an initial prototype, but

would require improvement for future iterations, both to improve ease of assembly and functional

capability.

Bend sensors appear to be an excellent candidate for a continuum arm. The low-cost approach

of a custom-made sensor demonstrates the robust nature of the design. Major improvements

currently needed are improved adhesion to the spine structure and a greater lateral flex ability.

Additionally, the resistance signal returned from the bend sensor is highly reliable, producing little

noise and good repeatability. Care needs to be taken to ensure the nominal resistance value is within

the micro-controller’s specification. Additional band-pass filtering should be investigated to further

improve performance.

The major outstanding issue with bend sensors is the lack of directionality. Each sensor will

change resistance in a direction-agnostic manner, and is thus unable to determine bend direction.

This can be resolved with a suitable control algorithm which compares the bend of all three sensors

simultaneously.

When mounting the nitinol actuators to the prototype single segment the resistance was found

to have increased significantly, from 1.5 ohms to 25 ohms. This demonstrates the strain-dependence of martensite, and required heat conditioning to reduce the resistance. During future construction,

prototypes would require similar conditioning before the expected heat cycling can be achieved.

Chapter 6 - Project Discussion

The results and methodology of the project are discussed and compared. A discussion on the

underlying causes for the primary issues are presented, and an evaluation of progress to resolution

of existing issues are analysed. Suggestions for potential solutions are presented, as are

recommendations for future study.

Modelling

As reported by Holschuh et. al. nitinol can be modelled as a spring. As demonstrated in this

project, the spring constant of nitinol is proportional to input power, effectively resulting in a spring

whose stiffness can be adjusted. This would allow for novel applications beyond a flexible robot;

for example collision reaction time can be drastically improved given the significantly higher

bandwidth of a spring as opposed to a conventional electric motor using back EMF as a force

feedback mechanism. This would prove beneficial for many human-robot interaction scenarios,

such as collaborative robots.

One of the most significant drawbacks, beyond the hysteresis and slow response issues, is the

extremely low efficiency of nitinol actuators. As these are essentially a heat engine, the theoretical

upper limit on efficiency is governed by the Carnot cycle, and maximum theoretical efficiency is

15%. The limiting factor within the Carnot cycle is generally the lowest achievable temperature

which, without any active cooling mechanism, would typically be only room temperature. Active

cooling using fluidics have been studied, but the consistent issues across all approaches are

increased size, weight and noise, which counteract the primary benefits of using a nitinol based

actuator design.

Limitations

Hysteresis remains the most significant hurdle to full development of a nitinol actuator system.

The heating cycle can be overcome through application of significant current for short periods,

however the cooling cycle is still problematic. As reported by O’Toole, smaller diameter nitinol

produces a faster response time, due to the decreased volume to surface ratio. Alternative

geometries,such as thin film nitinol, also offer potential for improved response.

One major limitation, as reported by Jani and encountered in this project, is uneven stress

distribution. In practise, this can be seen as an irregular coil pitch, caused by uneven martensite

formation, pockets of higher resistance, and consequent uneven joule heating. To resolve this, stress

must be kept constant across the nitinol coil, possibly with an additional mechanical structure, or

martensite formation must be conditioned during operation. This would most readily be achieved

with some insulating material, maintaining a consistent temperature across the entire actuator, or a

control system applying current to maintain even cooling. Both methods would negatively affect the

cooling response. A third option may be a selectively conductive element, such as a Peltier device or

other PN junction, which could be used to remove heat evenly from the nitinol.

Resistance acts as a potential sensing method for crystalline ratio. The most significant hurdle

to effective utilisation is the considerable noise encountered. An improved electronics design and

further study into effective filtering techniques is recommended. A major issue with using resistance

to determine crystalline ratio is the susceptibility to mechanical interference, which was found to

alter the sensed resistance value.

Additionally, the resistance of twinned martensite and austenite appear to be identical, which

may be caused by the shared crystalline structure. This would prevent any system from

distinguishing between the two crystalline phases.

At present, the precise cause of noise is not understood, though a link to strain and martensite

formation has been observed. Further study of the precise mechanism by which martensite and

austenite form is recommended.

A relatively slow heating cycle was encountered, due to the low current capability of the power

supply. Higher current capacities have been found to improve the heating cycle response and

effectively overcome heat cycle hysteresis, therefore future projects should use a higher current

power supply.

Reading the true value of resistance was found to be unnecessary. Using the raw ADC value

produces a relative value related to resistance, which was able to demonstrate repeatability, and

produced significantly less computational overhead, which is beneficial for development on a

platform with low computational power. The 10-bit resolution of the Atmega328’s on-board ADC

was found to provide sufficient resolution for detecting resistance change within nitinol.

Recommendations

To fully utilise nitinol in a control system a modelling approach is required. As reported by

Holschuh, Jani, Teh and many others, nitinol can be modelled as a spring, which experimentation in

this project confirms through the ability to extract a spring constant.

Testing of strain and stress was performed using a retort stand and masses. This produced

acceptable results, but more robust approaches are recommended, for example with use of a

universal test machine.

The single segment prototype was produced from low-cost readily available materials, and

serves as a functional test bed. However, several issues were found during construction. The

assembly is mostly maintained through tension and friction, which provides a critical failure point if

applied force is excessive. This should be remedied with improved fittings. The spine is constructed

from PVC tubing, which requires a compression spring to prevent buckling. The compression

spring also functions as a vital return mechanism against the nitinol. This compression spring needs

to be matched to the nitinol to optimise performance. Additionally, the compression spring adds

significant mass to the segment, which could affect performance, and was found to damage the

bend sensors during installation. For these reasons, a more integrated solution should be sought for

spine construction.

The bend sensors have proved to be a highly viable approach, and are recommended for future

projects, owing to accurate and repeatable measurements, ease of construction and integration.

During construction adhesion to the spine was only partially sufficient, and lateral flex was lower

than desired. These issues were partially solved with the compression spring aiding in sensor

retention, but future projects would be advised to improve adhesion and lateral flex.

Chapter 7 - Project Conclusions

The results of the project are summarised, with recommendations for future study outlined.

A high current controller was designed and constructed, and found to operate well. High current

is recommended to overcome the heating cycle hysteresis. Attempts at reading resistance to

determine crystalline ratio offer a potential avenue for power control, however significant noise was

encountered which rendered precise sensing infeasible, therefore further study into the cause of

noise in nitinol is recommended. A further complication is the identical resistance of austenite and

twined martensite, which would prevent a resistance based system from distinguishing between the

two crystalline forms.

One major previous issue is the low recoverable strain, typically around 4%. The coil type

actuator, used in the simple set up of this experiment, was still able to easily achieve 60% strain

recovery with a modest load and low power. The biggest issue is inconsistent uncoiling, which is

caused by the centre of the coil retaining more heat than the outermost coils, preventing the

formation of martensite, and therefore preventing even uncoiling.

The issue of low efficiency is one of the most significant hurdles to full utilisation of nitinol.

Ultimately the limiting factor comes as a result of being a heat engine, and most nitinol samples

cannot achieve lower than room temperature, due to lack of active cooling. Therefore, the lowest

temperature of nitinol needs to be reduced as far as possible to maximise efficiency, which would

require an active cooling system. Existing options of air or liquid are unsuitable due to increased

size, noise, weight and complexity, therefore an entirely novel approach is needed.

The most pressing issue of slow response is still outstanding. Ultimately, this is caused by the

hysteresis between martensite and austenite temperatures. During experimentation, applying a bias

spring resulted in improved actuation, and a noticeable oscillation was observed at a temperature of

40 Celsius and a load mass of 150 grams. These results may imply use of a bias load or antagonist

pair as a potential method for reducing the cooling cycle hysteresis and are recommended for future

study. Similar effects using the two-way shape memory effect were not investigated.

Controlling spring constant through manipulation of crystal ratios looks very promising.

Determining crystal ratios through resistance measurements offers a simple solution, but requires

significant improvement, primarily in filtering to remove noise. Other approaches might include

measurement of current draw or frequency response. More elaborate solutions may include

modifying the nitinol alloy such that the hysteresis loop is reduced, bringing the martensite finish

and austenite start temperatures closer together.

References

O'Toole, K. (2011) A Methodology Towards Comprehensive Evaluation of Shape Memory Alloy

Actuators for Prosthetic Finger Design. Doctoral Thesis. Dublin Institute of Technology

OCRobotics.com, 2012. LaserSnake2. [online]. Available at: http://www.ocrobotics.com/lasersnake2/ [Accessed 15th July 2018]

Teh, Y. (2008). Fast, Accurate Force and Position Control of Shape Memory Alloy Actuators.

Doctoral Thesis. The Australian National University.

Festo.com, 2011. BionicOpter. [online]. Available at: https://www.festo.com/group/en/cms/10224.htm [Accessed 15th July 2018]

Jani, J, Leary, M, Subic, A, Gibson, A. (2011) A review of shape memory alloy research,

applications and opportunities. Materials and Design, [online] Volume 56 (Issue 1), pages 1078-

1113. Available at: https://www.sciencedirect.com/science/article/pii/S0261306913011345 [Accessed 12th July 2018]

Kumar, P, Kumar, S. (2014). Shape memory Alloy (SMA) A Multi Purpose Smart Material. In:

National Conference on Synergetic Trends in engineering and Technology. International Journal of

Engineering and Technical Research, Special Issue (2014)

Ma, N, Song, G, Lee, H-J. (2004). Position control of shape memory alloy actuators with internal

electrical resistance feedback using neural networks, Smart Materials and Structures, Volume 1

(Issue 4), pages 777-783

Gorbet, R. (1996) A Study of the Stability and Design of Shape Memory Alloy Actuators. Master of

Applied Science. University of Waterloo.

Edge-tecind.com, 2015. Nitinol Fishing Wire. [online] Available at: http://www.edge-

techind.com/Products/Refractory-Metals/Titanium/Nitinol/Nitinol-Fishing-Wire-136-1.html (http://www.edge-techind.com/Products/Refractory-Metals/Titanium/Nitinol/Nitinol-Fishing-Wire-136-1.html) [accessed 17th
June 2018]

Zhang C, Zee RH, Thoma PE. Development of Ni-Ti based shape memory alloys for actuation and

control. In: Energy Conversion Engineering Conference 1996 (IECEC 96). IEEE; 1996. p. 239–44.

Holschuh, B, Obtropta E, Newman, D. “Low Spring Index NiTi Coil Actuators for Use in Active

Compression Garments.” IEEE/ASME Transactions on Mechatronics (2014): 1–14.

Lange, G, Lachmann, A, Rahim, A, Ismail, M, Low, C. (2015) Shape Memory Alloys as Linear

Drives in Robot Hand Actuation, Procedia Computer Science Volume 76 (Issue 1), pages 168 – 173

Qiu J, Tani J, Osanai D, Urushiyama Y. High-speed actuation of shape memory alloy. Smart Mater

MEMS: Int Soc Opt Photonics 2001:188–97.

Featherstone R, Teh Y. Improving the speed of shape memory alloy actuators by faster electrical

heating. In: Ang Jr M, Khatib O, editors. Experimental robotics IX. Berlin Heidelberg: Springer;

2006. p. 67–76.

Chee Siong L, Yokoi H, Arai T. New shape memory alloy actuator: design and application in the

prosthetic hand. in: 27th Annual International Conference of the Engineering in Medicine and

Biology Society (IEEE-EMBS 2005). Shanghai, China; 2005. p. 6900–3.

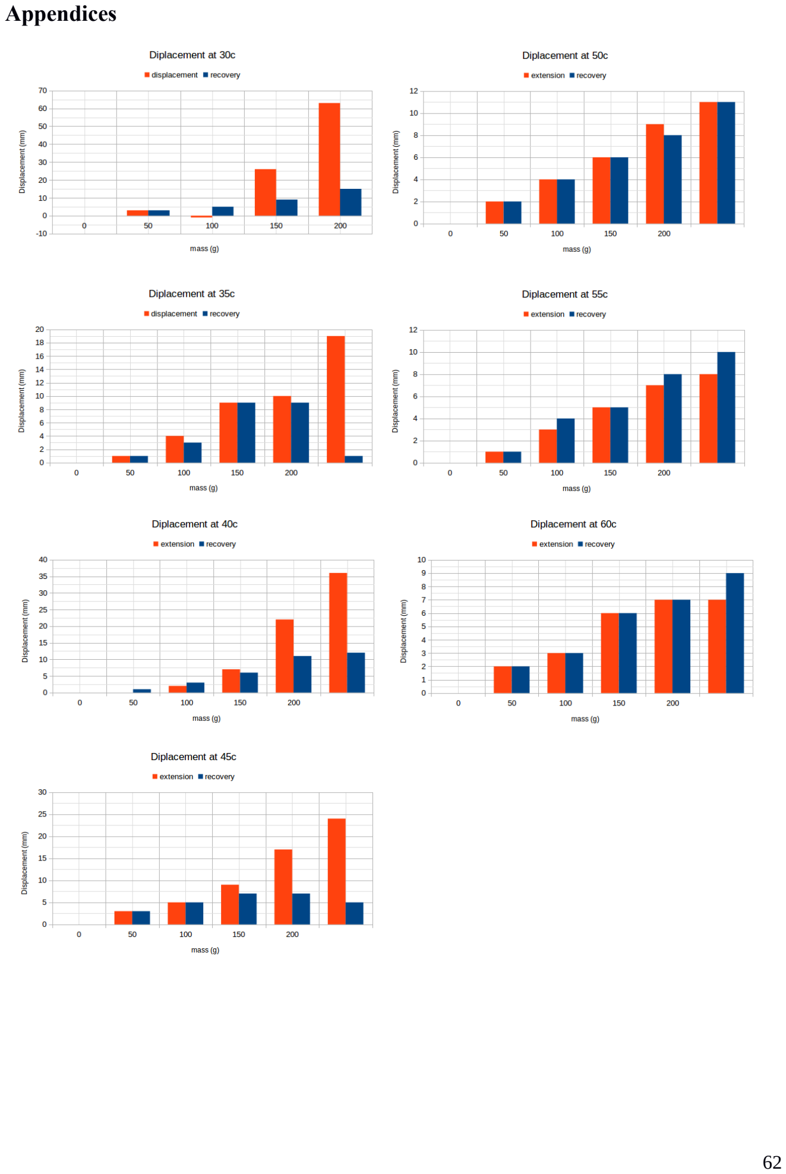
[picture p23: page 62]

Appendices

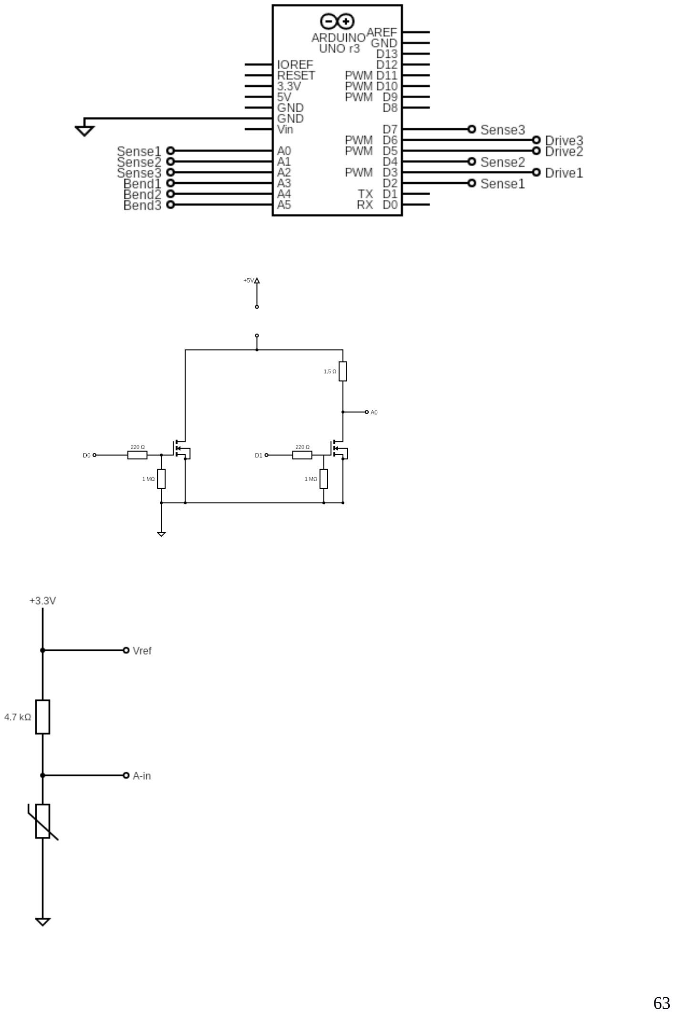
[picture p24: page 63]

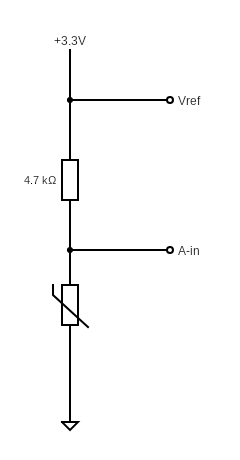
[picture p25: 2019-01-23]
electronics & software/temperature-circuit.png

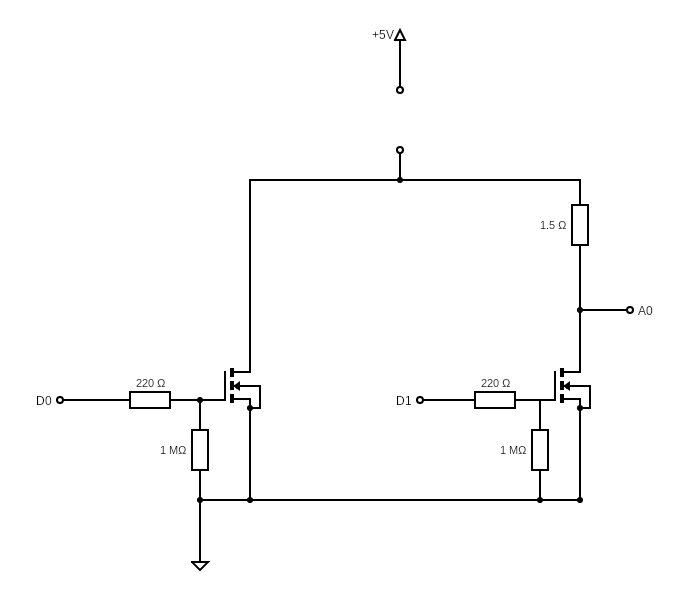
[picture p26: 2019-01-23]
electronics & software/driver-circuit.png

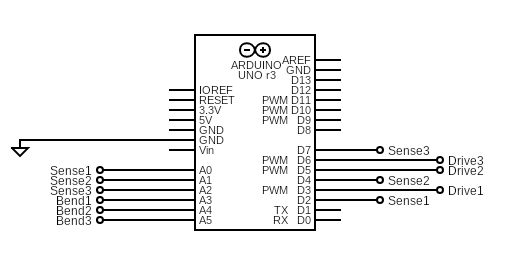
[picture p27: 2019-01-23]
electronics & software/controller-circuit.png

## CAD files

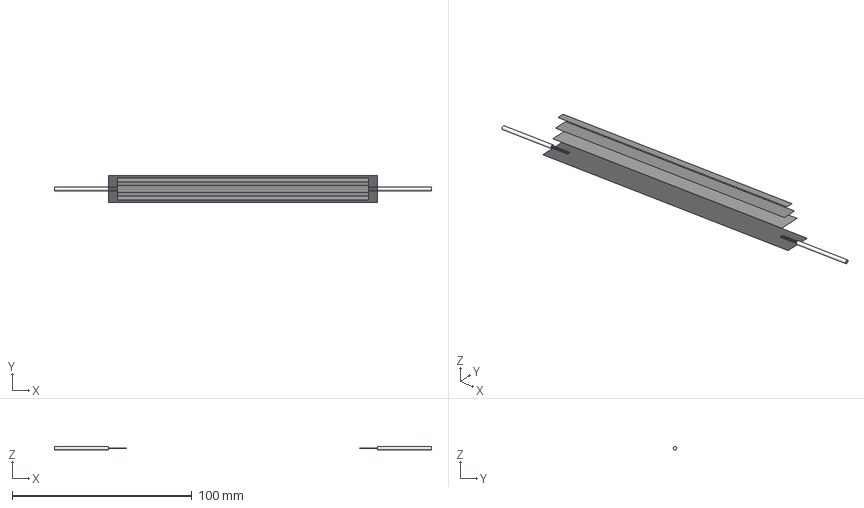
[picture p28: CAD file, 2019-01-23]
hardware/bend sensor diagram.fcstd
210.0 x 15.0 x 20.0 mm
Rectangle
Rectangle001
Rectangle002
Rectangle003

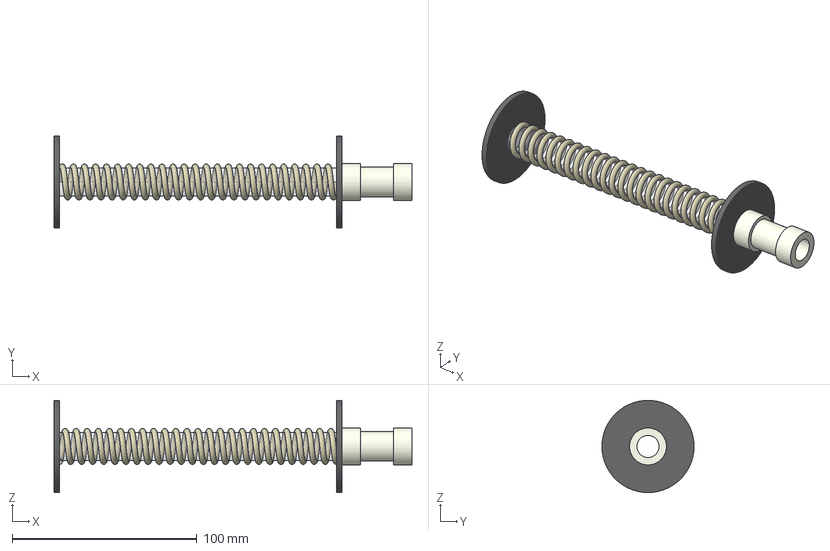
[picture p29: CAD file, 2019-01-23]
hardware/spine.fcstd
194.0 x 50.0 x 50.0 mm
spring

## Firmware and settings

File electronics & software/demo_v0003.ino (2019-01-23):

/*  June 30th 2018
    Simple bang-bang controller
    Extended to measure ersistance by voltage drop
*/

//Definitions
#define THERMISTORPIN A0        //Analogue pin thermistor is on
#define RESISTANCEPIN A1
#define NUMSAMPLES 5            //Number of samples to read and average, more is slower but smoother
#define THERMISTORNOMINAL 10000 //Resistance at 25c, Thermistor NJ28NA0103F, rs part number 697-4576
#define TEMPERATURENOMINAL 25   //Tempeature for nominal resistance (should pretty much always be 25c)
#define BCOEFFICIENT 4100       //Beta coefficient for Steinhart-hart equation
#define SERIESRESISTOR 9860     //Value of current-limiting resistor, measure with DMM
const float SENSERESISTOR = 1.6; //Sense resistor, as measured. Nitinol will be somewhere between 1.5 and 3 ohms at room temperature

int samples[NUMSAMPLES];        //Initialise array for averaging
int samplesvIn[NUMSAMPLES];
int samplesvOut[NUMSAMPLES];
int holdtemp;               //Timer to hold temperature for 9 seconds

bool driverON = false;                  //Flag for driver circuit being ON or OFF
bool max_achieved = false;
bool min_achieved = false;

#define NIT_PIN_1 8              //Nitinol driver pin
#define NIT_PIN_2 9
#define NIT_PIN_3 10
#define SENSEPIN_1 11             //Nitinol sensor pins
#define SENSEPIN_2 12
#define SENSEPIN_3 13

#define MAX_TEMP 50
#define MIN_TEMP 40

float bend_sensor_rest;
float bend_sensor_max;

void setup() {  
  Serial.begin(9600);
  analogReference(EXTERNAL);    //Cconnect AREF to 3.3V and use that as VCC, less noisy!

  pinMode(NIT_PIN_1, OUTPUT);
  pinMode(NIT_PIN_2, OUTPUT);
  pinMode(NIT_PIN_3, OUTPUT);
  digitalWrite(NIT_PIN_1, LOW);
  digitalWrite(NIT_PIN_2, LOW);
  digitalWrite(NIT_PIN_3, LOW);
  pinMode(SENSEPIN_1, OUTPUT);
  pinMode(SENSEPIN_2, OUTPUT);
  pinMode(SENSEPIN_3, OUTPUT);
  digitalWrite(SENSEPIN_1, LOW);
  digitalWrite(SENSEPIN_2, LOW);
  digitalWrite(SENSEPIN_3, LOW);

  
  bend_sensor_rest = analogRead(A0);  //throw-away reading to stabilise ADC
  delay(1);   
  bend_sensor_rest = analogRead(A0);

  bend_sensor_max = bend_sensor_rest*1.1;    //Will move to +10% of resting position

}

/*-------------------------------------------------------------------------------------------------------------------------------
 Main loop
-------------------------------------------------------------------------------------------------------------------------------*/

void loop() {
  //float temperature;
  float bend_value;
  //temperature = read_temperature();
  //calcResist();
  bend_value = read_bend();
  apply_current(bend_value);
  Serial.println(); //To seperate each trace
  delay(10);
}

/*-------------------------------------------------------------------------------------------------------------------------------
 Read temperature. Read n ADC values, average to reduce noise, convert to resistance, temperature via Steinhart equation
 https://learn.adafruit.com/thermistor/using-a-thermistor
-------------------------------------------------------------------------------------------------------------------------------*/
float read_temperature() {
  uint8_t i;
  float average;

  // take N samples in a row, with a slight delay
  for (i = 0; i < NUMSAMPLES; i++) {
    samples[i] = analogRead(THERMISTORPIN);
    delay(5);
  }

  // average all the samples out
  average = 0;
  for (i = 0; i < NUMSAMPLES; i++) {
    average += samples[i];
  }
  average /= NUMSAMPLES;

  // convert the value to resistance
  average = 1023 / average - 1;
  average = SERIESRESISTOR / average;

  //Convert to celsius
  float steinhart;
  steinhart = average / THERMISTORNOMINAL;          //(R/R0)
  steinhart = log(steinhart);                       //ln(R/R0)
  steinhart /= BCOEFFICIENT;                        //1/B
  steinhart += 1.0 / (TEMPERATURENOMINAL + 273.15); //+1/T0)
  steinhart = 1.0 / steinhart;
  steinhart -= 273.15;                              //convert to C

  Serial.print("Thermistor = "); Serial.print(steinhart); Serial.print("          "); //whitespace
  return steinhart; //return steinhart as temperature
}

/*-------------------------------------------------------------------------------------------------------------------------------
  http://robotics.hobbizine.com/flexinolresist.html
  calcResist takes ADC readings at A0 and A1, converts them to voltages and uses the results to
  calculate the resistance of the Flexinol - the constant value of 0.004883 used here is equal to
  the reference voltage of 5 divided by the ADC resolution of 1024
  CHANGES: Using A1 and A2 (A0 for thermistor), using 3.3Vref, so const is 3.3/1024 = 0.003222656
  Float has 7 points of precision, so 0.003223
  Only read single analogue value, six pins can then measure 3 nitinol resistance values and 3 strain gauges
-------------------------------------------------------------------------------------------------------------------------------*/

float calcResist(){
  //Really needs some noise filtering
  //Needs to be called on interrupt routine maybe every 500ms - 1000ms to avoid heating nitinol
  uint8_t i;
  float average;
  float vIn;
  float vOut;
  float rFlexinol_1;
  float rFlexinol_2;
  float rFlexinol_3;
  
  digitalWrite(SENSEPIN_1, HIGH); //Turn mosfet on so we have a voltage to read
  digitalWrite(SENSEPIN_2, HIGH);
  digitalWrite(SENSEPIN_3, HIGH);
  
  if (driverON == false){        //turning driver circuit on drops current to sensing device, V=IR, sensitivity increased
    digitalWrite(NIT_PIN_1, HIGH);
    digitalWrite(NIT_PIN_2, HIGH);
    digitalWrite(NIT_PIN_3, HIGH);
  }
  /*
   * //Filtered analogue reading
 
  
  for(i=0; i < NUMSAMPLES; i++){
    vIn = analogRead (A1);   //take a throw-away reading to reset the ADC after switching pins
    delay (10);
    samplesvIn[i] = analogRead (A1);

    vOut = analogRead (A2);   //take a throw-away reading to reset the ADC after switching pins
    delay (10);
    samplesvOut[i] = analogRead (A2);
  }
  */

  //Unfiltered analogue reading
  rFlexinol_1 = analogRead (A3);   //take a throw-away reading to reset the ADC after switching pins
  delay (10);
  rFlexinol_1 = analogRead (A3);

  rFlexinol_2 = analogRead (A4);
  delay (10);
  rFlexinol_2 = analogRead (A4);

  rFlexinol_3 = analogRead (A5);  
  delay (10);
  rFlexinol_3 = analogRead (A5);
  
  digitalWrite(SENSEPIN_1, LOW);  //Disable ASAP so as not to heat nitinol
  digitalWrite(SENSEPIN_2, LOW);
  digitalWrite(SENSEPIN_3, LOW);
  if (driverON == true){        //Turn driver back on if it was on
    digitalWrite(NIT_PIN_1, HIGH);
    digitalWrite(NIT_PIN_2, HIGH);
    digitalWrite(NIT_PIN_3, HIGH);
  }

  /*
  // average all the vIn samples
  average = 0;
  for (i = 0; i < NUMSAMPLES; i++) {
    average += samplesvIn[i];
  }
  average /= NUMSAMPLES;
  vIn = average;

  // average all the vOut samples
  average = 0;
  for (i = 0; i < NUMSAMPLES; i++) {
    average += samplesvOut[i];
  }
  average /= NUMSAMPLES;
  vOut = average;
  */
  
  /*
  //Convert to voltage
  vIn = vIn * 0.003223;
  vOut = vOut * 0.003223;
  
  //rFlexinol = (SENSERESISTOR * vOut) / (vIn - vOut);
  rFlexinol = (vIn / vOut) - 1;
  rFlexinol = rFlexinol * SENSERESISTOR;
  Serial.print("Resistance = "); Serial.println(rFlexinol);
  return rFlexinol;
  */

  Serial.print(rFlexinol_1); Serial.print(" "); Serial.print(rFlexinol_2); Serial.print(" "); Serial.print(rFlexinol_3);  Serial.print(" ");
}

/*-------------------------------------------------------------------------------------------------------------------------------
Read bend sensors
Use raw ADC values, actual resistance has no bearing on position, just wastes machine cycles

-------------------------------------------------------------------------------------------------------------------------------*/
float read_bend(){
  //Read bend sensor resistance
  float bend_sensor_1;
  float bend_sensor_2;
  float bend_sensor_3;
  
  bend_sensor_1 = analogRead(A0);  //throw-away reading to stabilise ADC
  delay(1);   
  bend_sensor_1 = analogRead(A0);

  bend_sensor_2 = analogRead(A1);  //throw-away reading to stabilise ADC
  delay(1);   
  bend_sensor_2 = analogRead(A1);
  
  bend_sensor_3 = analogRead(A2);  //throw-away reading to stabilise ADC
  delay(1);   
  bend_sensor_3 = analogRead(A2);
  
  Serial.print(bend_sensor_1); Serial.print(" ");  Serial.print(bend_sensor_2); Serial.print(" "); Serial.print(bend_sensor_3); Serial.print(" ");
  return bend_sensor_3;
}

/*-------------------------------------------------------------------------------------------------------------------------------
 Bang-bang controller, incorporate Teh's work later
 At very high ferquencies, especially with PID, rise and fall times may become crucial. At the moment, MOSFET will turn and
 off faster than arduino
 May be good idea to implement flag variable, so calcResist function knows if MOSFET needs to be turned on
 
 Need to actuate nitinol 2 and 3 (as wired to stripboard)
-------------------------------------------------------------------------------------------------------------------------------*/
void apply_current(float bend_value) {  

  if ((bend_value<bend_sensor_max) && (!max_achieved)){
    digitalWrite(NIT_PIN_2, HIGH);
    digitalWrite(NIT_PIN_3, HIGH);
    driverON = true;
    Serial.println("Power on");
  }

  if (bend_value>=bend_sensor_max){
    max_achieved = true;
    min_achieved = false;
  } 
  
  if ((bend_value>bend_sensor_rest) && (max_achieved)){
    digitalWrite(NIT_PIN_2, LOW);
    digitalWrite(NIT_PIN_3, LOW);
    driverON = false;
    Serial.println("Power off");
  }

  if (bend_value<bend_sensor_rest){
    min_achieved = true;
    max_achieved = false;
  } 
}
